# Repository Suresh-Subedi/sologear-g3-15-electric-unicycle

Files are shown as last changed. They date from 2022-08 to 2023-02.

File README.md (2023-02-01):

# Sologear G3-15 Electric Unicycle
Sologear G3-15 Electric Unicycle reverse engineering to reuse motherboard with custom firmware.
Schematics of other generic cheaper electric unicycles (monowheels) should be same/similar. Let us know in the issues.

### Running code
Install Platform IO extension in VS Code.
Open firmware folder in VS Code
Connect programmer (without connecting 3.3V)
Switch monowheel on

Monowheel folder contains KiCad files for the monowheel.

### Ports
#### P2
|Pin|Marking|Comment |
|---|---|---|
|1  |5V | |
|2  | |Not connected|
|3  |SPK | |

Connected in parallel with buzzer

#### P3 Power switch LED
|Pin|Marking|Comment|
|---|---|---|
|1  | |5V |
|2  | | |
|3  | | |

#### P4 Hall sensor
|STM32F103C8T6|Hall sensor|Color |Comment |
|---|---|---|---|
| |1 |Black |GND |
|PA0 |2 |Blue  | |
|PA1 |3 |Yellow| |
|PA2 |4 |Green | |
| |5 |Red |5V |

#### P5 Battery indicator
From switch to charging connector: 1 - 4
|STM32F103C8T6|P4 Battery Indicator|Color |Comment |
|---|---|---|---|
|PA15 |1 |Black |Via resistor R1|
|PB4 |2 |Blue  |Via resistor R2|
|PB5 |3 |Yellow|Via resistor R3|
|PB8 |4 |Green |Via resistor R4|
| |5 |Red |+5V |

#### P6
|Pin|Marking|Comment|
|---|---|---|
|1  | |PA4 via R6 10k resistor|
|2  | |GND |

#### P7 Power switch ON OFF PWR
|Pin|Marking|Comment |
|---|---|---|
|1  | |+60V |
|2  | |To board |

#### SWD
|STM32F103C8T6|SWD|
|---|---|
|PA14 |SWC|
|PA13 |SWD|
| |3V3|
| |GND|

[Bill of materials](https://docs.google.com/spreadsheets/d/1EM--kQIaX84T2JI6LrDOyGJttcWCDYOLsfqfUfqGejQ/edit?usp=sharing)

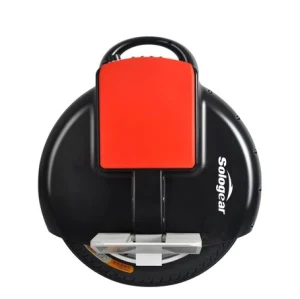
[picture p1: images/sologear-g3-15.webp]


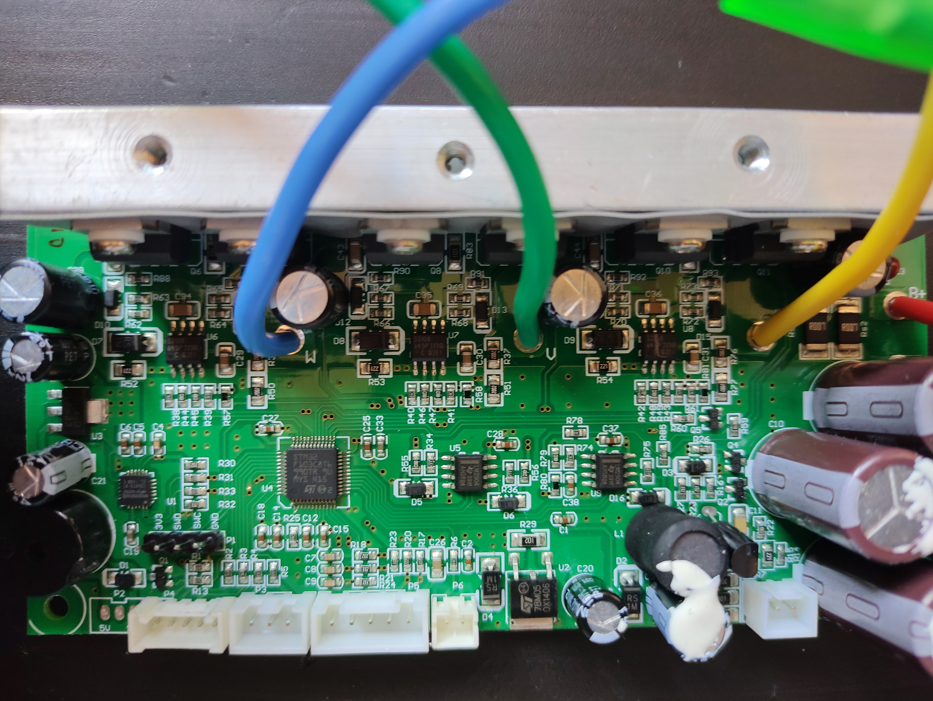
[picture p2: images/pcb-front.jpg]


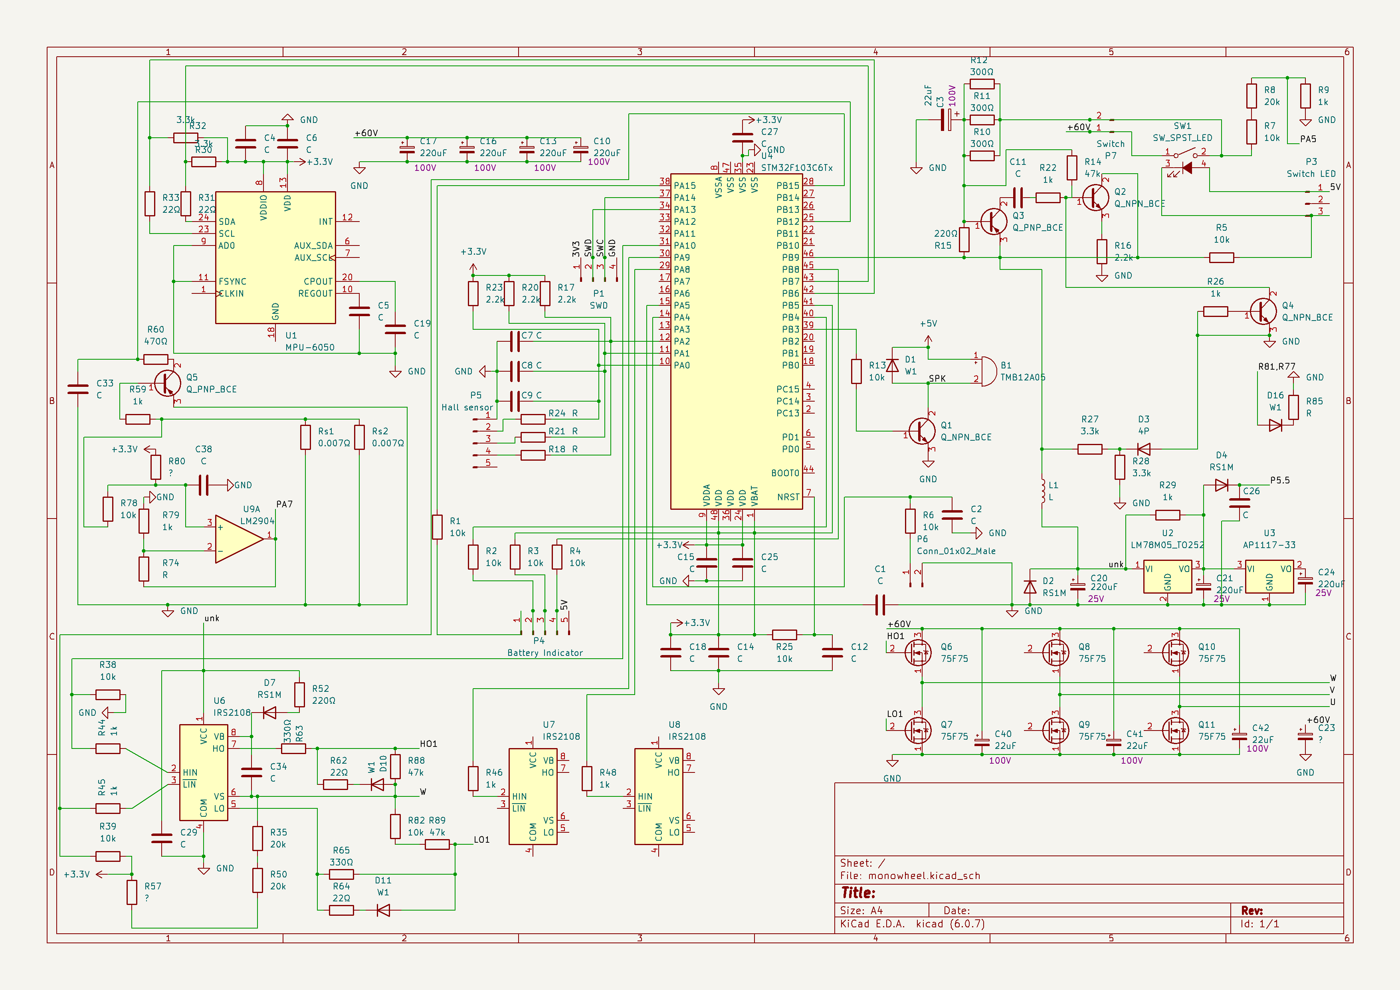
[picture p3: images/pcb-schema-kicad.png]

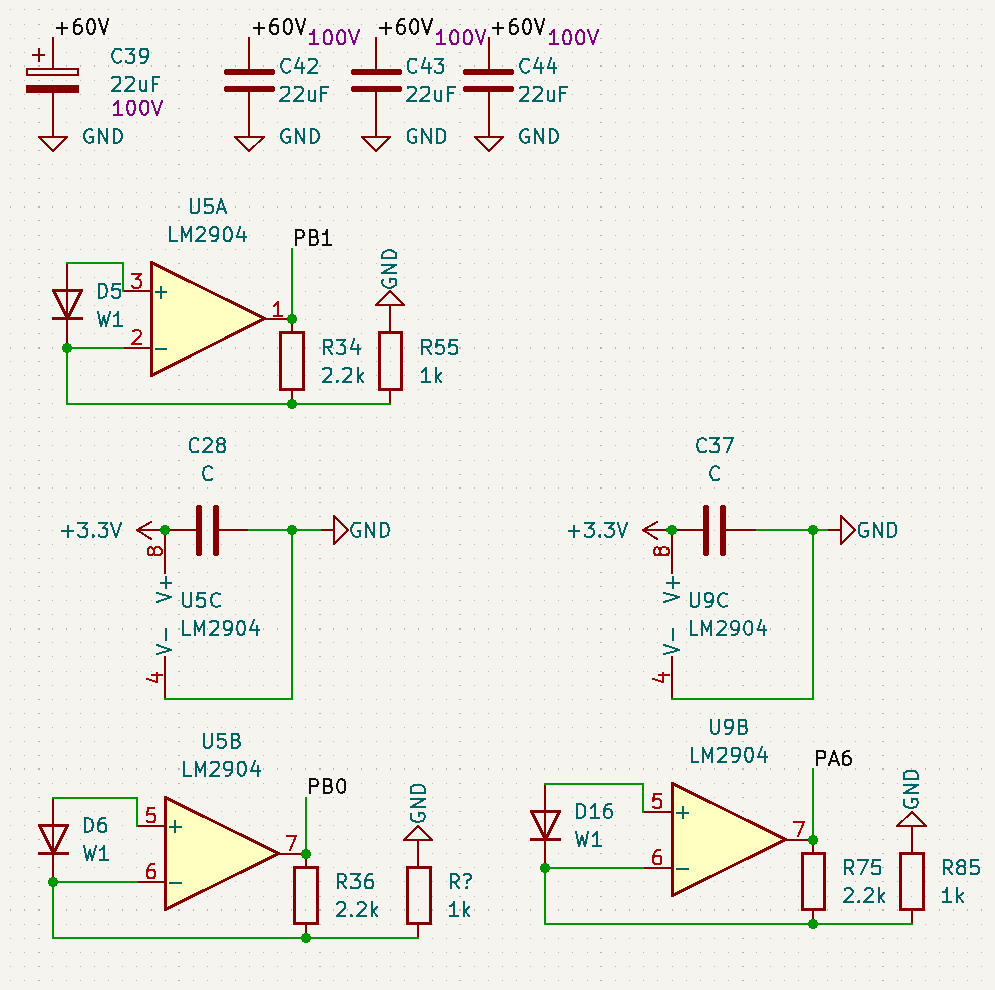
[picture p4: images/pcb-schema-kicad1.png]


|Step|1 |2 |3 |4 |5 |6 |
|----|----|----|----|----|----|----|
|High|A |B |B |C |C |A |
|Low |C |C |A |A |B |B |
| |H1L3|H2L3|H2L1|H3L1|H3L2|H1L2|

https://www.digikey.be/nl/articles/what-is-the-most-effective-way-to-commutate-a-bldc-motor
https://www.digikey.nl/en/blog/using-bldc-hall-sensors-as-position-encoders-part-1
| |U  |V  |W  |Step|
|-|---|---|---|----|
|1|+  |-  |off|6 |
|2|+  |off|-  |1 |
|3|off|+  |-  |2 |
|4|-  |+  |off|3 |
|5|-  |off|+  |4 |
|6|off|-  |+  |5 |
| |A  |B  |C  | |

#### Connections
|STM32F103C8T6|MPU 6050|Comment |
|---|---|---|
|PB7 |SDA |Via resistor R31|
|PB6 |SCL |Via resistor R33|

Half-Bridge Driver connections
|STM32F103C8T6|IRS2108 |
|---|---|
|PB10 |HIN1 |
|PB09 |HIN2 |
|PB08 |HIN3 |
|PB15 |LIN1 |
|PB14 |LIN2 |
|PB13 |LIN3 |

### Firmware
Existing firmware was unprotected and could be read using STM-Link V2. Soldering headers was a bit difficult as pin holes were already filled with solder.

### Components
STM32F103C8T6\
InvenSense MPU 6050\
6 MOSFET ST P75NF75&\
[IRS2108 Half-bridge Driver](https://www.infineon.com/dgdl/irs2108.pdf?fileId=5546d462533600a40153567649d627a8) 8-Lead SOIC

### Battery
59.2V/4.4Ah 260Wh SAMSUNG/22PM\
Hy-LYX-1602B-22PM-144900042

### Motor
CST e-BIKE PRO Li-ion Electronic\
14AMK1512615052\
XINAOMA

### Useful software
STM32 ST-LINK Utility\
Ghidra with SVD-Loader

### Connections
|Marking on board|Connections|Connected |
|---|---|---|
|P2 |2 |5v SPK Unpopulated |
|P3 |3 |2p connected to switch LED |
|P4 |5 |2mm: battery level |
|P5 |5 |2.5mm: hall effect sensor |
|P6 |2 |Disconnected |
|P7 |2 |Switch |
#### Switch
|Marking on board|Color|Switch|
|---|-----|---|
|P3 |Red  | |
|P3 |Black| |
|P7 |Red  | |
|P7 |White|Center|

#### Charging port
Red
Black
Connected to battery
#### Motor connection
|Color |Marking on board|
|---|---|
|Yellow|Y? |
|Green |V |
|Blue  |W |

???
GND
3.3V

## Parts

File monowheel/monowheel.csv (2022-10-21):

Source: | C:\Users\ssubedi\Documents\monowheel\monowheel.kicad_sch
Date: | 01/08/2022 19:55:10
Tool: | Eeschema (6.0.7)
Generator: | C:\Program Files\KiCad\6.0\bin\scripting\plugins/bom_csv_grouped_by_value_with_fp.py
Component Count: | 78
Ref | Qnty | Value | Cmp name | Footprint | Description | Vendor
B1, | 1 | TMB12A05 | Buzzer |  | Buzzer, polarized
C3, C31, C39, C40, C41, | 5 | 22uF | C_Polarized_Small |  | Polarized capacitor, small symbol
C7, C8, C9, C26, C29, C34, C42, | 7 | C | C |  | Unpolarized capacitor
C10, C13, C16, C17, C20, C21, C24, | 7 | 220uF | C_Polarized_Small |  | Polarized capacitor, small symbol
C23, | 1 | ? | C_Polarized_Small |  | Polarized capacitor, small symbol
D7, | 1 | RS1M | D |  | Diode
D10, D11, | 2 | W1 | D |  | Diode
P1, | 1 | SWD | Conn_01x04_Male |  | Generic connector, single row, 01x04, script generated (kicad-library-utils/schlib/autogen/connector/)
P3, | 1 | Switch LED | Conn_01x03_Male |  | Generic connector, single row, 01x03, script generated (kicad-library-utils/schlib/autogen/connector/)
P4, | 1 | Battery Indicator | Conn_01x05_Male |  | Generic connector, single row, 01x05, script generated (kicad-library-utils/schlib/autogen/connector/)
P5, | 1 | Hall sensor | Conn_01x05_Male |  | Generic connector, single row, 01x05, script generated (kicad-library-utils/schlib/autogen/connector/)
P6, | 1 | Conn_01x02_Male | Conn_01x02_Male |  | Generic connector, single row, 01x02, script generated (kicad-library-utils/schlib/autogen/connector/)
P7, | 1 | Switch | Conn_01x02_Male |  | Generic connector, single row, 01x02, script generated (kicad-library-utils/schlib/autogen/connector/)
Q2, | 1 | Q_PNP_BCE | Q_PNP_BCE |  | PNP transistor, base/collector/emitter
Q6, Q7, Q8, Q9, Q10, Q11, | 6 | 75F75 | 2N7000 | Package_TO_SOT_THT:TO-92_Inline | 0.2A Id, 200V Vds, N-Channel MOSFET, 2.6V Logic Level, TO-92
R1, R2, R3, R4, R5, R6, R38, R39, R82, | 9 | 10k | R |  | Resistor
R10, R11, R12, | 3 | 300Î© | R |  | Resistor
R18, R21, R24, | 3 | R | R |  | Resistor
R31, R33, R62, R64, | 4 | 22Î© | R |  | Resistor
R35, R50, | 2 | 20k | R |  | Resistor
R44, R45, R46, R48, | 4 | 1k | R |  | Resistor
R52, | 1 | 220Î© | R |  | Resistor
R57, | 1 | ? | R |  | Resistor
R63, R65, | 2 | 330Î© | R |  | Resistor
R88, R89, | 2 | 47k | R |  | Resistor
Rs1, Rs2, | 2 | 0.007Î© | R |  | Resistor
SW1, | 1 | SW_SPST_LED | SW_SPST_LED |  | Single Pole Single Throw (SPST) switch with LED, generic
U1, | 1 | MPU-6050 | MPU-6050 | Sensor_Motion:InvenSense_QFN-24_4x4mm_P0.5mm | InvenSense 6-Axis Motion Sensor, Gyroscope, Accelerometer, I2C
U2, | 1 | LM78M05_TO252 | LM78M05_TO252 | Package_TO_SOT_SMD:TO-252-2 | Positive 500mA 35V Linear Regulator, Fixed Output 5V, TO-252 (D-PAK)
U3, | 1 | AP1117-33 | AP1117-33 | Package_TO_SOT_SMD:SOT-223-3_TabPin2 | 1A Low Dropout regulator, positive, 3.3V fixed output, SOT-223
U4, | 1 | STM32F103C6Tx | STM32F103C6Tx | Package_QFP:LQFP-48_7x7mm_P0.5mm | ARM Cortex-M3 MCU, 32KB flash, 10KB RAM, 72MHz, 2-3.6V, 37 GPIO, LQFP-48
U6, U7, U8, | 3 | IRS2108 | IRS2108 |  | Half-Bridge Driver, 600V, 290/600mA, PDIP-8/SOIC-8

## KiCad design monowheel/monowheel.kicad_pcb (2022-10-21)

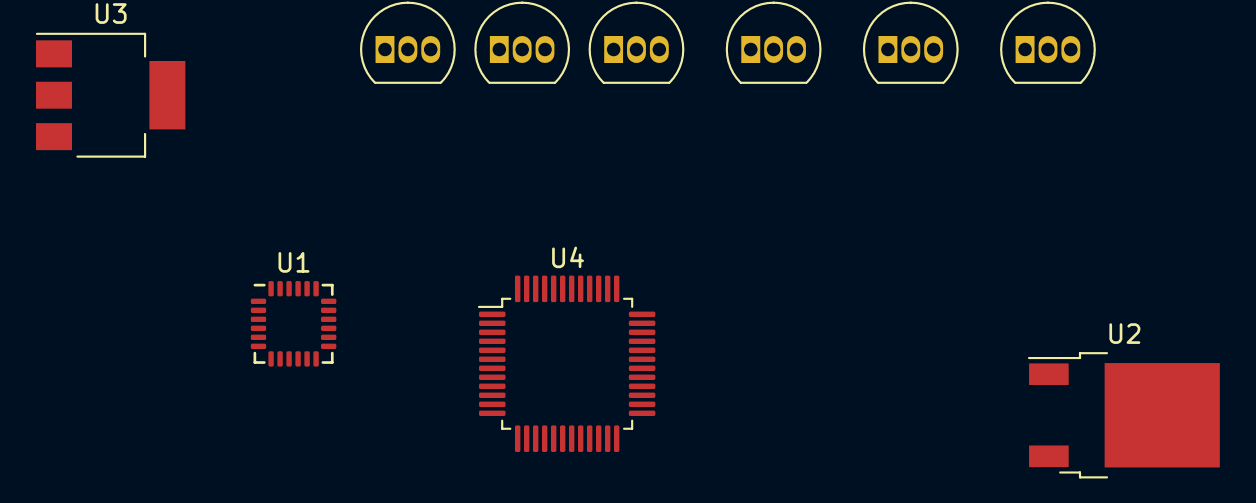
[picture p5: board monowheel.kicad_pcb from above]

Board: 2 copper layers, 10 parts (0 on the bottom side), 5 nets, no tracks yet.

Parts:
Q6, Q7, Q8, Q9, Q10, Q11: 75F75; TO-92_Inline
U1: MPU-6050; InvenSense_QFN-24_4x4mm_P0.5mm
U2: LM78M05_TO252; TO-252-2
U3: AP1117-33; SOT-223-3_TabPin2
U4: STM32F103C6Tx; LQFP-48_7x7mm_P0.5mm

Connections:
/U: Q10.1 (S), Q11.3 (D)
/V: Q8.1 (S), Q9.3 (D)
/W: Q6.1 (S), Q7.3 (D)
unnamed: Q7.1 (S), Q9.1 (S), Q11.1 (S)
unnamed: Q6.3 (D), Q8.3 (D), Q10.3 (D)

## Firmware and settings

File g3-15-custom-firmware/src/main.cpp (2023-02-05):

#include <Arduino.h>

// Hall-effect sensor 3.3V
int HS1 = PA0; // Blue Pin 2
int HS2 = PA1; // Yellow Pin 3
int HS3 = PA2; // Green Pin 4

int led1 = PA15;
int led2 = PB4;
int led3 = PB5;
int led4 = PB8;
int leds[] = { led1, led2, led3, led4 };
// int leds[] = { led4, led3, led2, led1 };
int powerLed = PB9;

void setup () {  
  pinMode(HS1, INPUT);
  pinMode(HS2, INPUT);
  pinMode(HS3, INPUT);

  pinMode(powerLed, OUTPUT);

  // LEDs
  pinMode(led1, OUTPUT);
  pinMode(led2, OUTPUT);
  pinMode(led3, OUTPUT);
  pinMode(led4, OUTPUT);
}

void display(byte number) {
  for(byte i = 0; i < 4; i++) {
    bool value = number & 1;
    digitalWrite(leds[i], !value);
    number /= 2;
  }
}

byte i = 0;

void loop() {
  digitalWrite(powerLed, LOW);

  int angle = analogRead(HS1);
  display(i);
  i += 1;
  i = i % 16;
  delay(1000);
}

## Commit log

2022-10-21 add kicad files
    [monowheel.csv, monowheel.kicad_pcb, monowheel.kicad_sch]
2023-02-01 add code to control buzzer and leds
    [main.cpp]
